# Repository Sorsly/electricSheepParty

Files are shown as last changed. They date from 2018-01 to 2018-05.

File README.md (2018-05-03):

# esp
Our senior design project, Electronic Sheep Party.
## Steps to Run
* Turn on LAN (Make sure all bots are configured to connect)
* Set up camera above the bots
* power cycle each bot and wait for the green light to turn off
* run `putilov getIP`, wait
* run `putilov run`, select y
* Launch your two seprate game front ends
* play game

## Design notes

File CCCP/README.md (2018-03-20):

Note: The Id slice in CCCP maps integers 0->numbots to camera defined ID numbers.
      The frontend only knows the bots id in the form of the index in this ids slice
      The camera only knows the distinct id it gives the blobs it sees
      The CCCPs jobs is to keep those two numbers in check, and assign the right values to the correct index

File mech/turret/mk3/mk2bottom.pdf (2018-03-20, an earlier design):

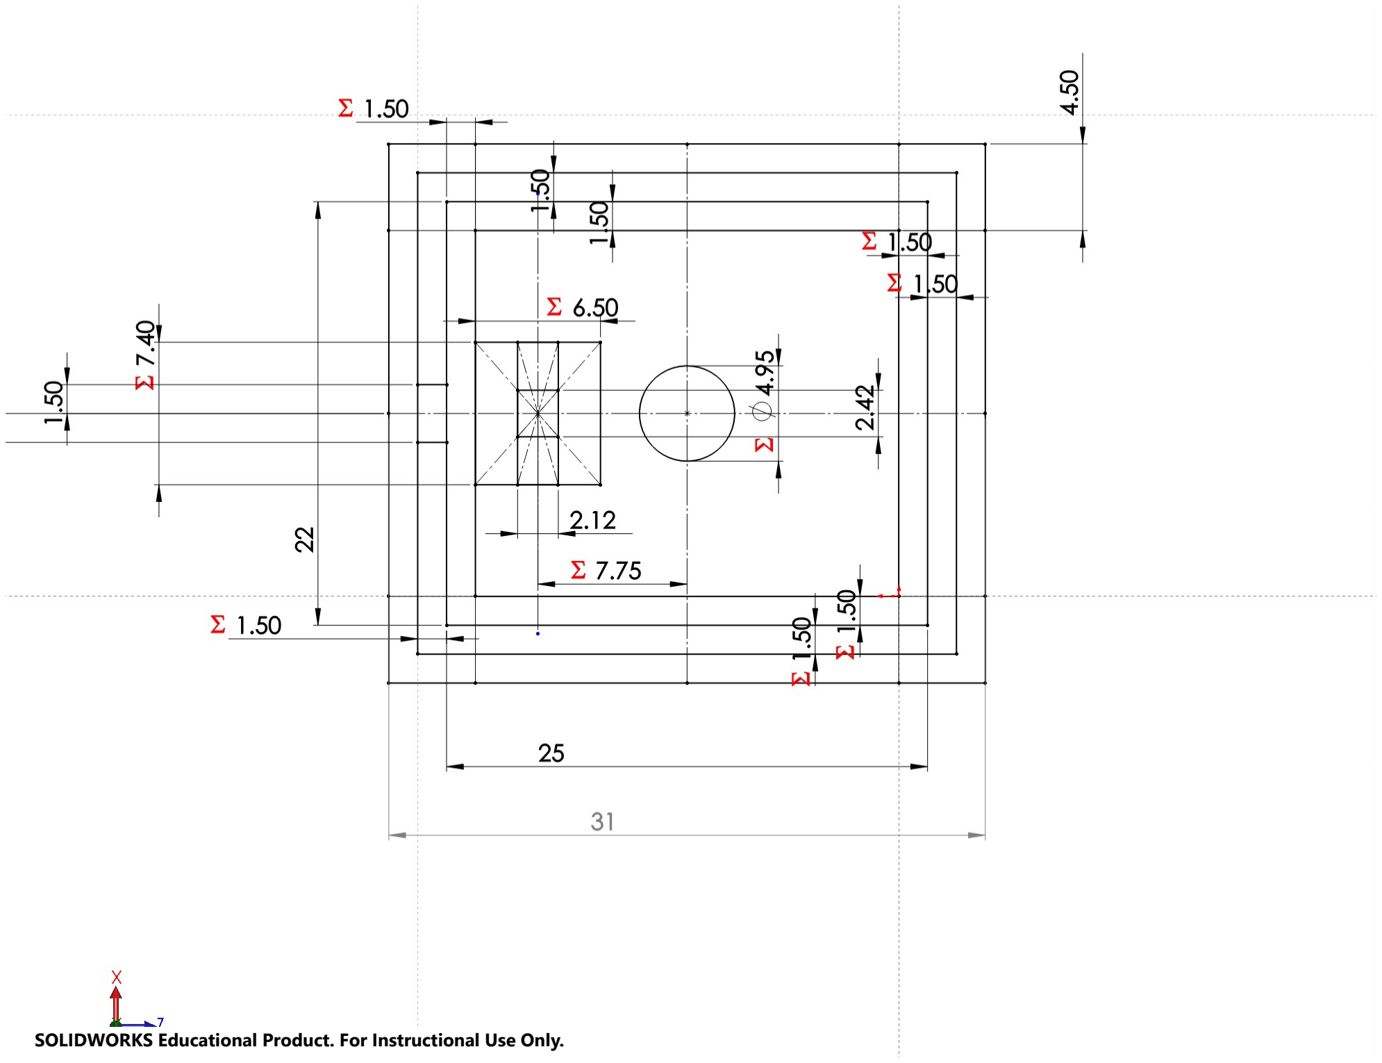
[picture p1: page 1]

SOLIDWORKS Educational Product. For Instructional Use Only.

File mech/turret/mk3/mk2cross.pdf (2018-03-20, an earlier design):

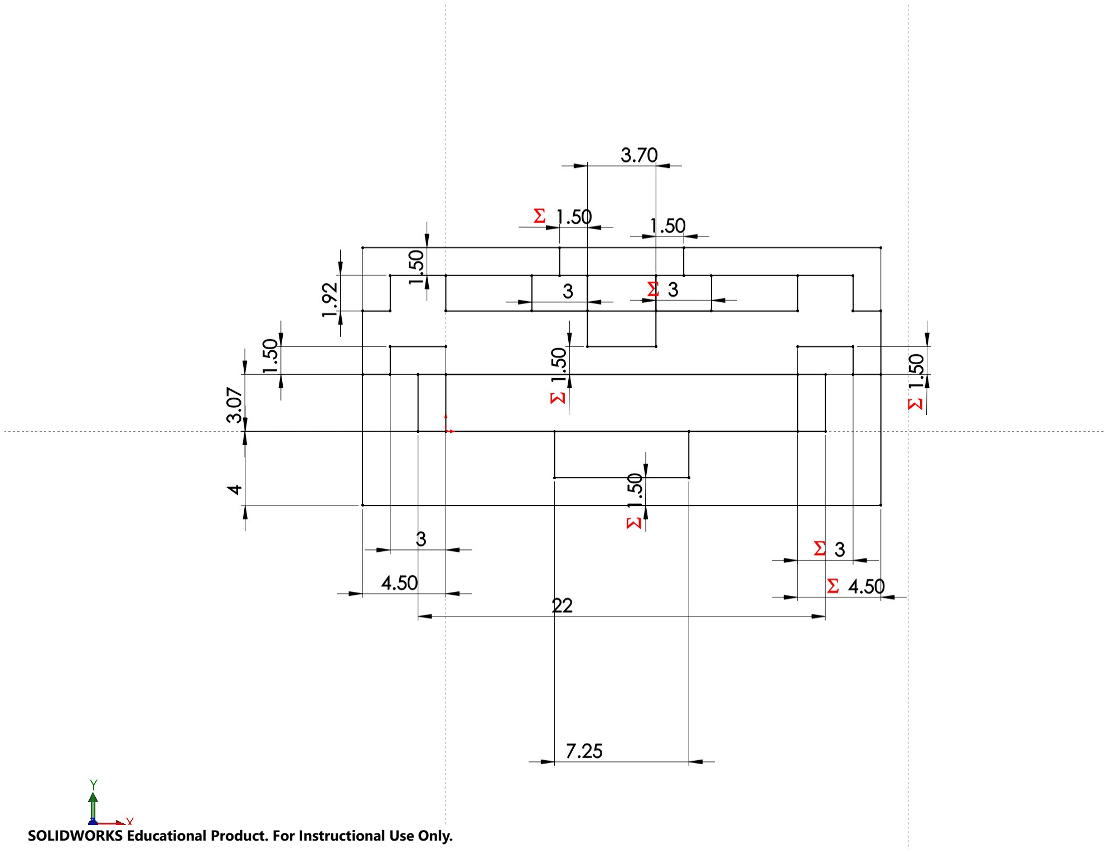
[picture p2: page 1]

SOLIDWORKS Educational Product. For Instructional Use Only.

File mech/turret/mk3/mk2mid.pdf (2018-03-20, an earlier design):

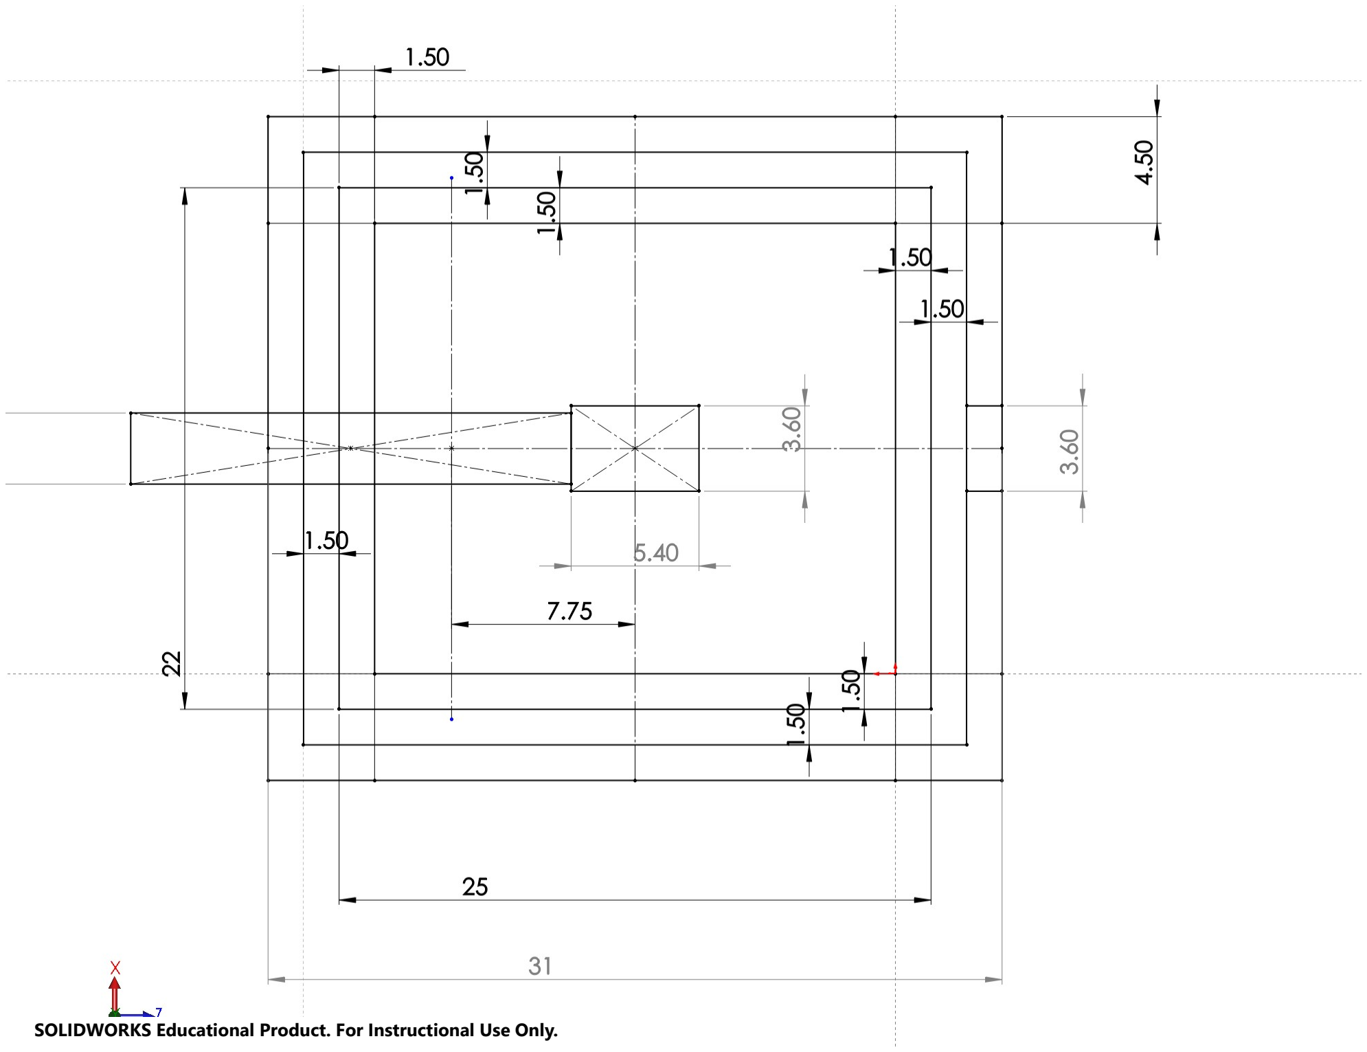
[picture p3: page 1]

SOLIDWORKS Educational Product. For Instructional Use Only.

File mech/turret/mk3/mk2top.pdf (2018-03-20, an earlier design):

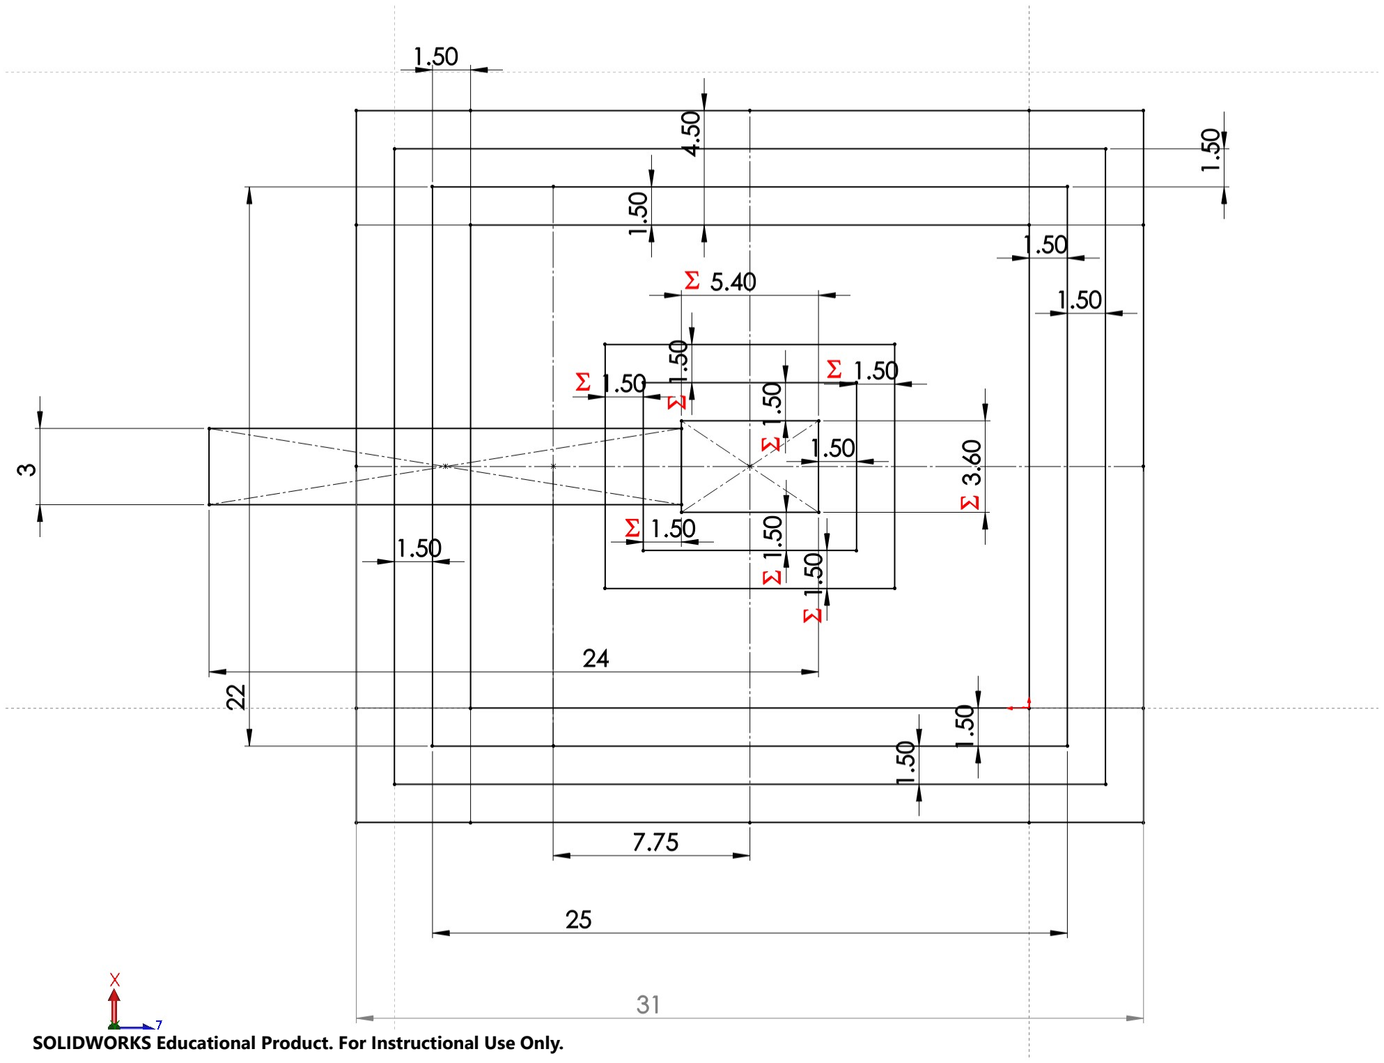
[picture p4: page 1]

SOLIDWORKS Educational Product. For Instructional Use Only.

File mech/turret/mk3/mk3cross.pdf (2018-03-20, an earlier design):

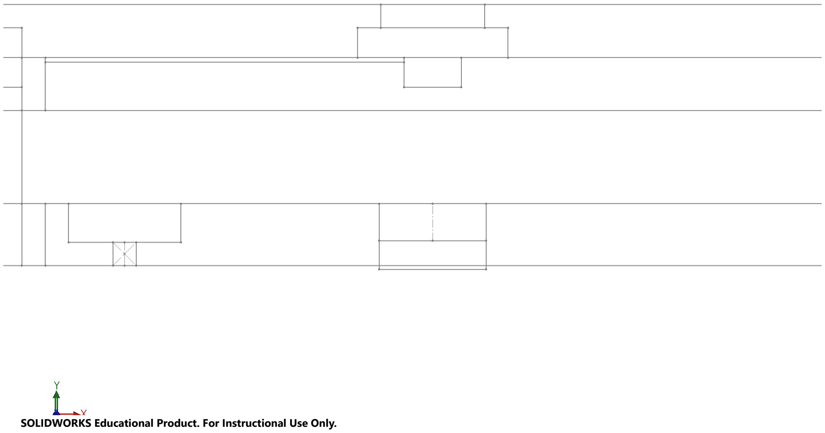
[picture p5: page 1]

SOLIDWORKS Educational Product. For Instructional Use Only.

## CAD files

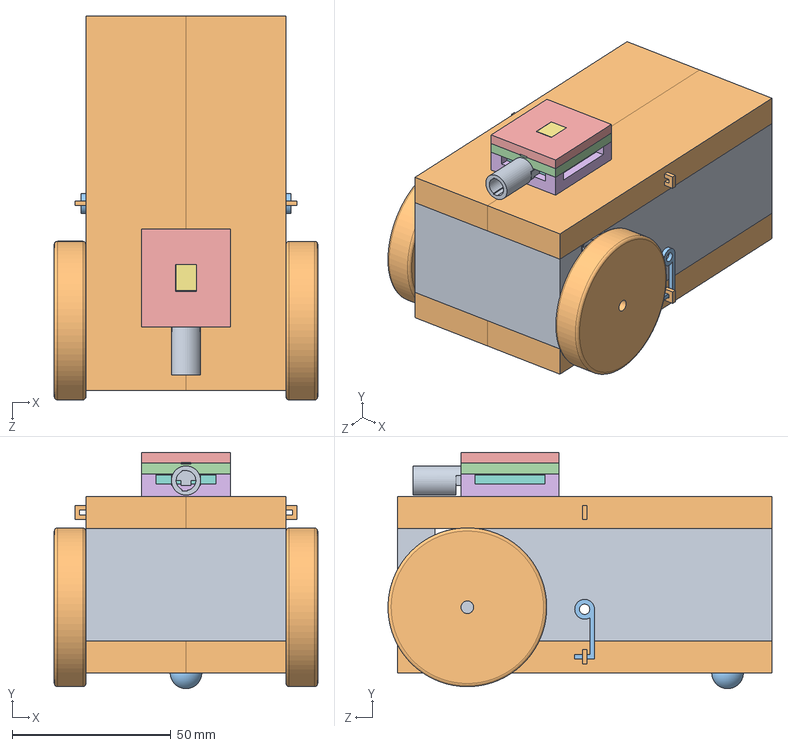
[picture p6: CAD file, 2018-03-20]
mech/asm/mechOverview.SLDASM
83.0 x 74.4 x 120.9 mm
Base 4.0 v9
pcb holder v5 x 2
J hook v2 x 2
turretBodyMiddle
turretBodyTop
turretBodyBottomSLDPRT
turretBodyTopLedCover
turretAcryllic
turretGun
drivePlaceholder x 2
thirdPlaceholder

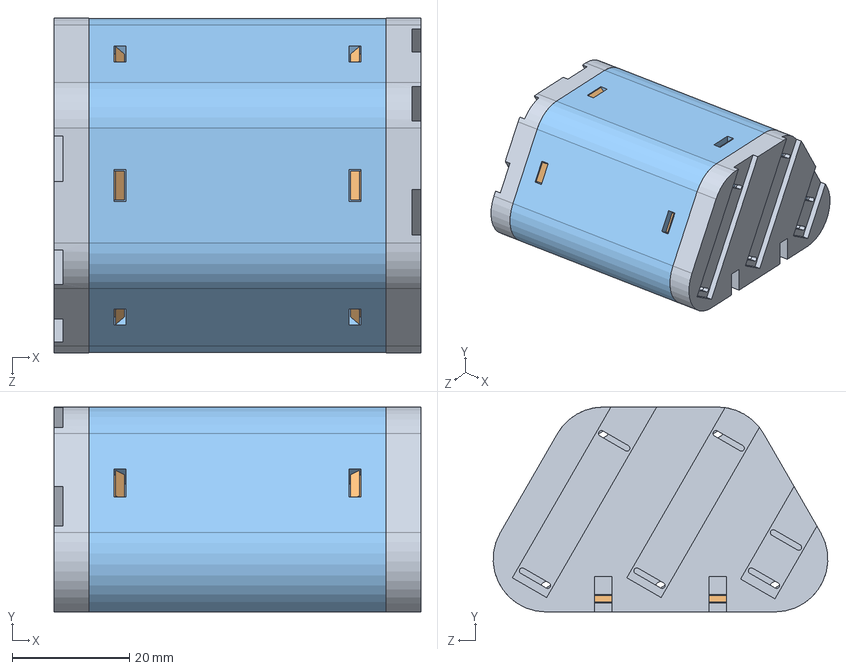
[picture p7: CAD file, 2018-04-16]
mech/body/mk3 (rev4)/batteryHousing/batteryHousingDetachable.SLDASM
62.5 x 34.9 x 57.0 mm
batteryCapDetachable x 2
batteryCant x 10
batteryShell

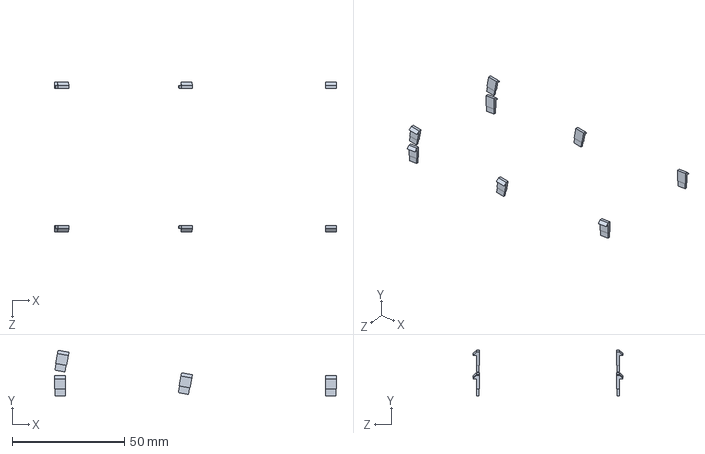
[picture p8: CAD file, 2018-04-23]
mech/body/mk3 (rev4)/bodyTop.SLDASM
125.8 x 20.3 x 67.0 mm
batteryCant x 8

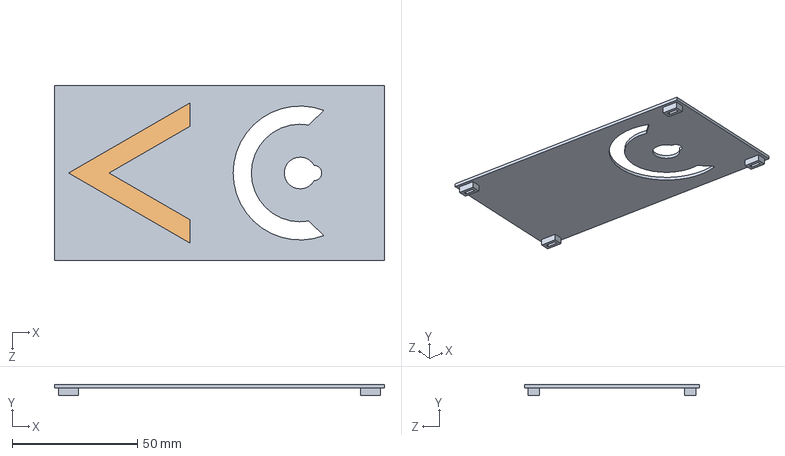
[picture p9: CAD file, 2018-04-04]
mech/body/mk3 (rev4)/bodyTopCV/bodyTopCV.SLDASM
131.9 x 4.50 x 70.0 mm
bodyTop
markCV

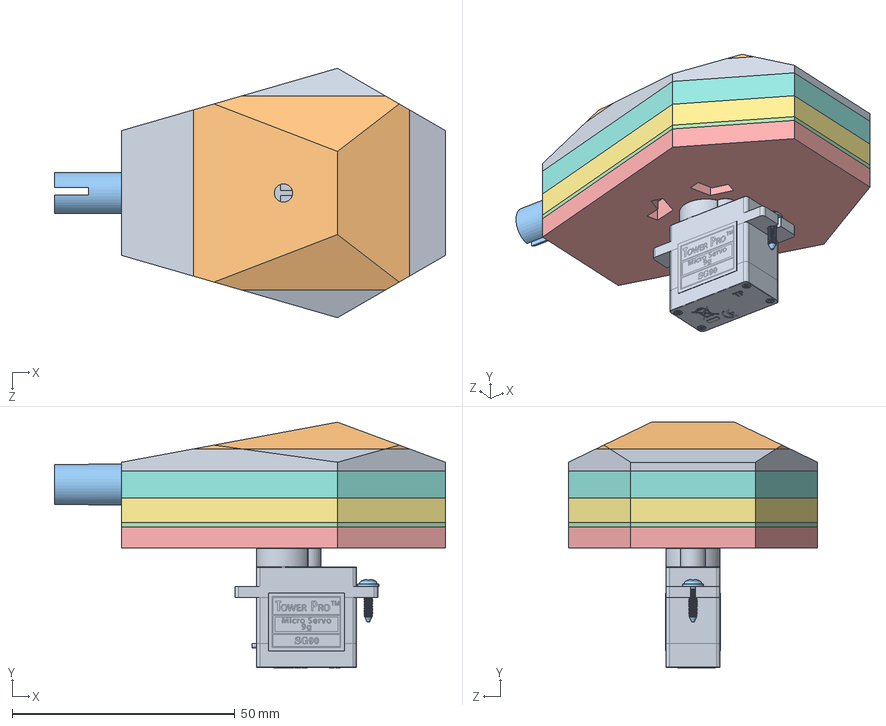
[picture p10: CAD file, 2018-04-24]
mech/turret/mk4/turret_mk4.SLDASM
87.8 x 55.2 x 56.0 mm
turretGround
quadFin
turretLevel1
turretLevel2_diffuser
turretLevel3
turretPenthouse
turretGun_fromMk3
finScrewAdjust

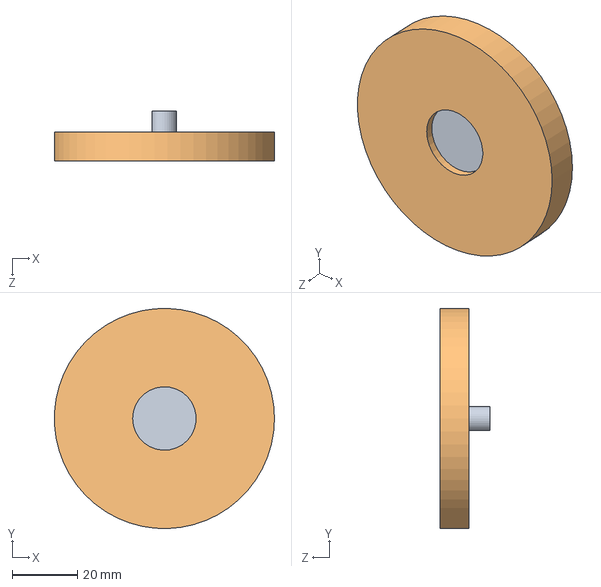
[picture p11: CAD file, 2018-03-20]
mech/wheels/mk3/wheel_mk3.SLDASM
67.4 x 67.4 x 15.4 mm
wheelCore
wheelTire

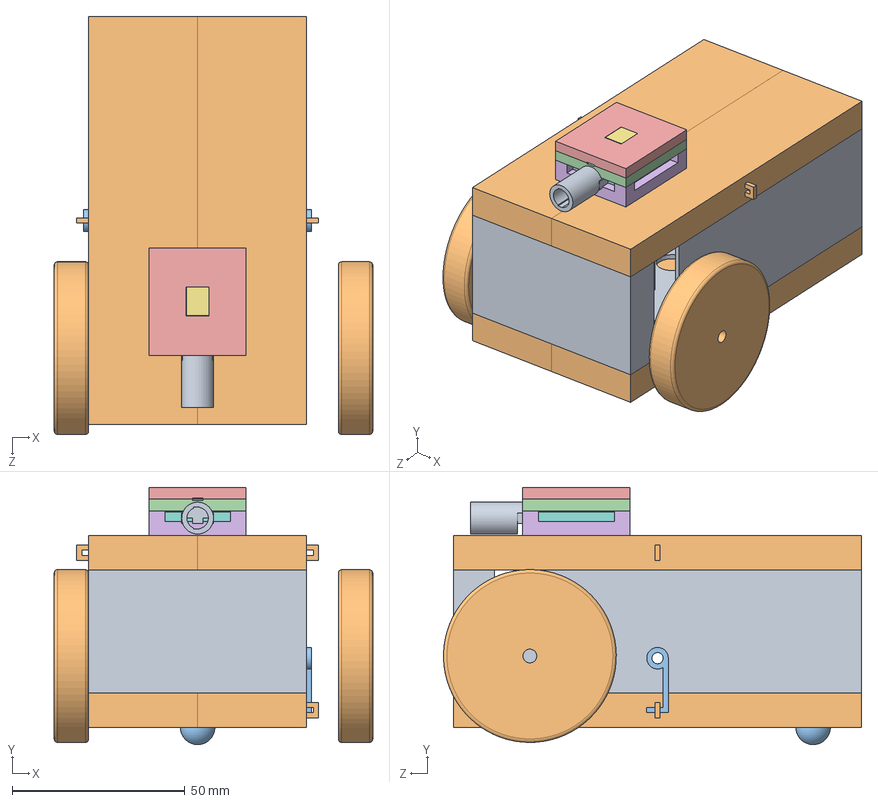
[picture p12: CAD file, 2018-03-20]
mech/asm/Backup (2) of mechOverview.SLDASM
92.2 x 74.4 x 120.9 mm
Base 4.0 v9
pcb holder v5 x 2
J hook v2 x 2
turretBodyMiddle
turretBodyTop
turretBodyBottomSLDPRT
turretBodyTopLedCover
turretAcryllic
turretGun
drivePlaceholder x 2
thirdPlaceholder

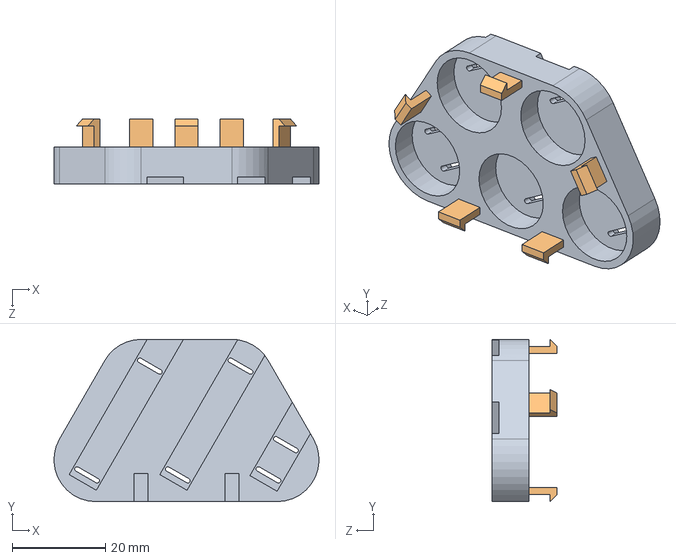
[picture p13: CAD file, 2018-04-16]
mech/body/mk3 (rev4)/batteryHousing/batteryCapDetachableInclCant.SLDASM
57.0 x 34.9 x 14.0 mm
batteryCapDetachable
batteryCant x 5

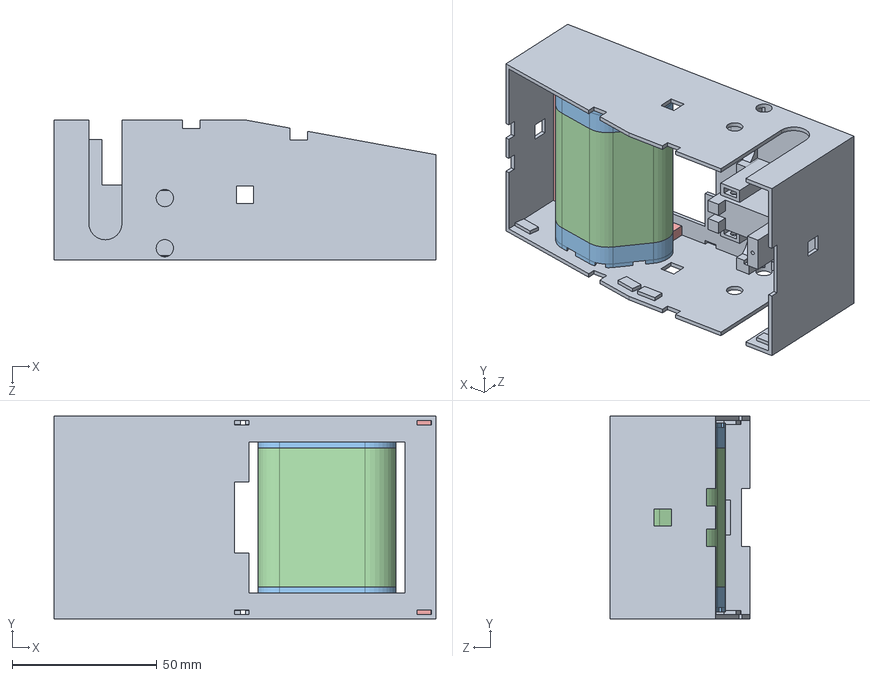
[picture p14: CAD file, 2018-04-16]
mech/body/mk3 (rev4)/fixes/cableSpacingHotFix.SLDASM
131.9 x 70.0 x 48.4 mm
batteryCap_mk3.5 x 2
batteryShell_mk3.5
slantFix

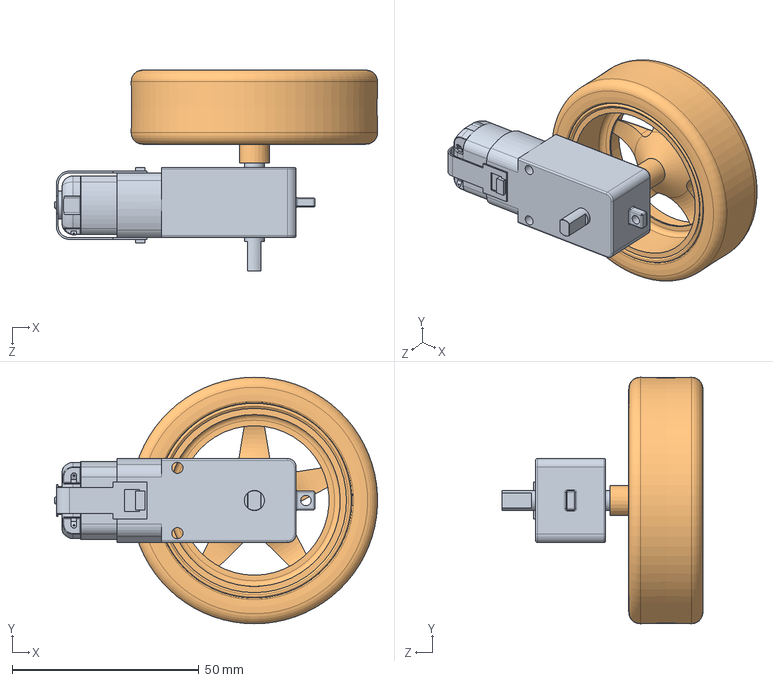
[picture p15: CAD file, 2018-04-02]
mech/misc/moto-reductor-rueda-1.snapshot.1/Moto Reductor - Rueda.SLDASM
86.5 x 66.0 x 53.9 mm
Moto Reductor 01
Rueda 01

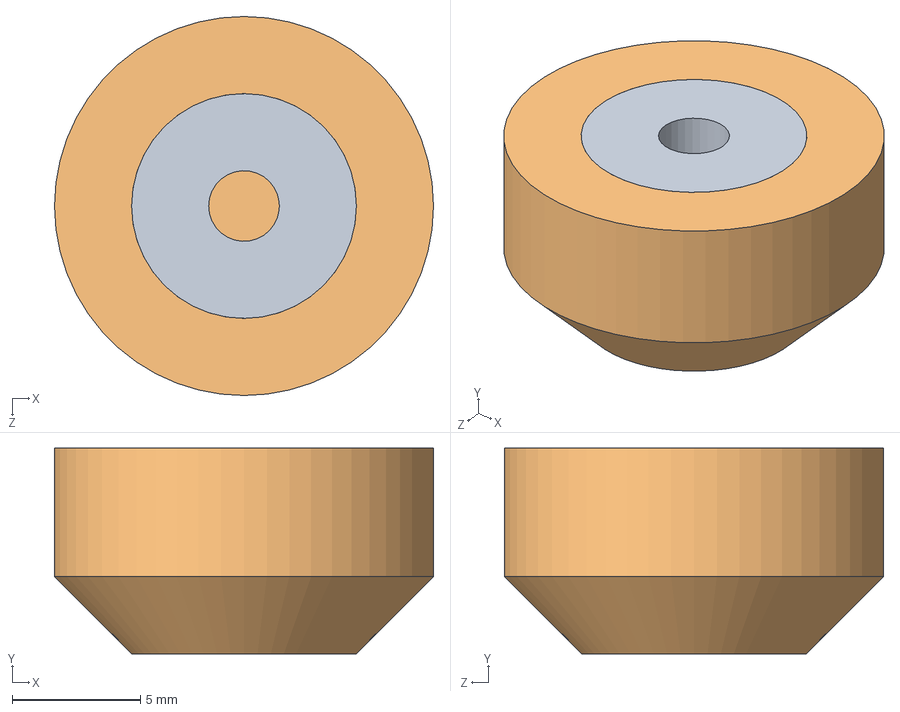
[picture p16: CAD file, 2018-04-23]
mech/wheels/mk3.5/omni/omniFoot.SLDASM
14.8 x 8.00 x 14.8 mm
maleNub
foot

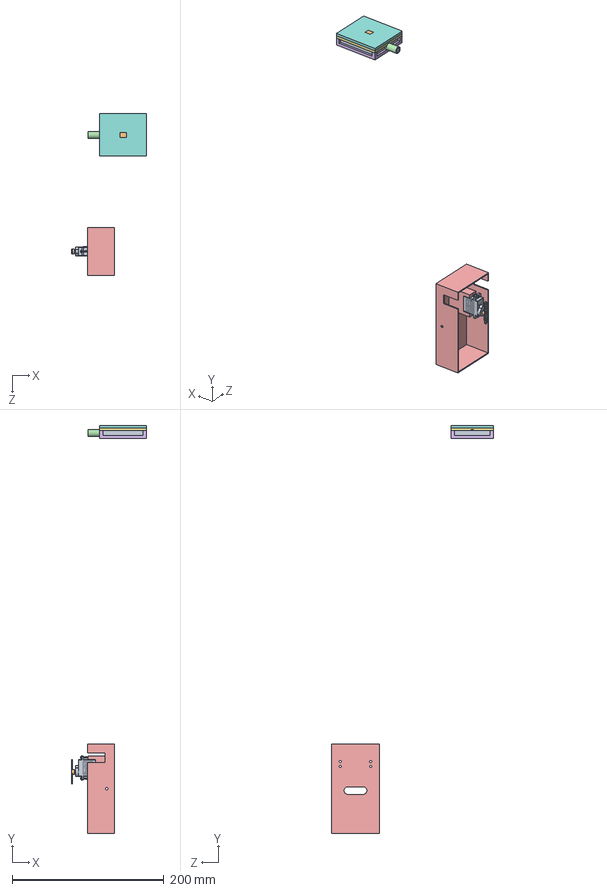
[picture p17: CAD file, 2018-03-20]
mech/asm/master.SLDASM
99.1 x 537.0 x 213.1 mm
SG90 - Micro Servo 9g - Tower Pro.1
SG90 - Micro Servo 9g - Tower Pro.3
SG90 - Micro Servo 9g - Tower Pro.5 x 2
SG90 - Micro Servo 9g - Tower Pro.6
Base 4.0 v10_mk2
turretBottom
turretMid
turretTop
turretDiffuser
turretLEDcover
Part10^turretGun

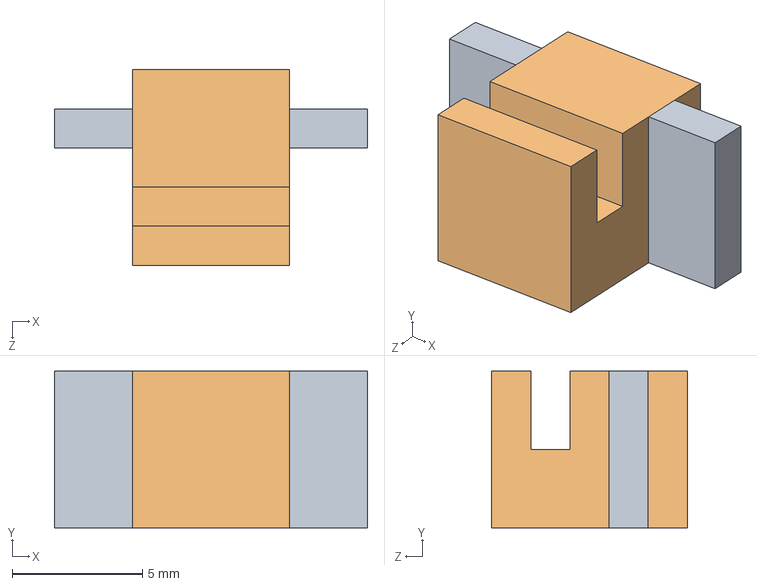
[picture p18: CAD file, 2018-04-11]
mech/body/mk3 (rev4)/attachPoint/Backup (1) of attachPointASM.SLDASM
12.0 x 6.00 x 7.50 mm
attachPoint
attachHook

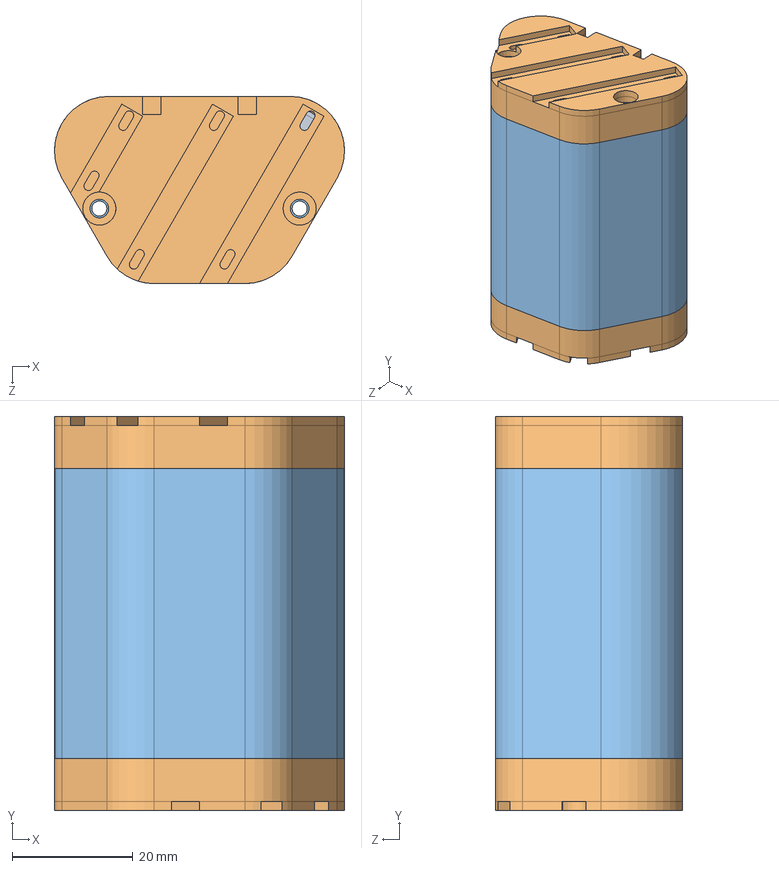
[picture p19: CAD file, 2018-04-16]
mech/body/mk3 (rev4)/batteryHousing/mk3.5/batteryHousing_mk3.5.SLDASM
48.0 x 65.2 x 31.0 mm
batteryCap_mk3.5 x 2
batteryShell_mk3.5

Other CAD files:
mech/wheels/mk3/omni/omniASM.sldasm
mech/misc/sg90-micro-servo-9g-tower-pro-1.snapshot.2/SG90 - Micro Servo 9g - Tower Pro.SLDASM
mech/misc/team/espPin.SLDASM
mech/misc/utility/aBox.SLDASM
mech/asm/Backup (1) of mechOverview.SLDASM
mech/asm/Backup (3) of mechOverview.SLDASM
mech/body/Base 2.0 v7.step
mech/body/Base 4.0 v2.step
mech/body/mk3 (rev4)/Backup (1) of bodyTop.SLDASM
mech/body/mk3 (rev4)/Backup (1) of bodyTop.sldprt
mech/body/mk3 (rev4)/Backup (1) of body_mk3.sldprt
mech/body/mk3 (rev4)/Backup (1) of frontWeightContainer.sldprt
mech/body/mk3 (rev4)/Backup (1) of omniBallCore.sldprt
mech/body/mk3 (rev4)/Backup (1) of pcbHolder_mk3.sldprt
mech/body/mk3 (rev4)/Backup (1) of protoBody.SLDASM
mech/body/mk3 (rev4)/Backup (2) of bodyTop.SLDASM
mech/body/mk3 (rev4)/Backup (2) of body_mk3.sldprt
mech/body/mk3 (rev4)/Backup (2) of frontWeightContainer.sldprt
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

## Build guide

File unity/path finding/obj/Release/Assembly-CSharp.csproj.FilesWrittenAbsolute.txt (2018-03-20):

/Users/snayha/Unity/path finding/Temp/bin/Release/Assembly-CSharp.dll.mdb
/Users/snayha/Unity/path finding/Temp/bin/Release/Assembly-CSharp.dll
/Users/snayha/Unity/path finding/obj/Release/Assembly-CSharp.dll
/Users/snayha/Unity/path finding/obj/Release/Assembly-CSharp.dll.mdb
/Users/snayha/Unity/path finding/Temp/bin/Release/UnityEngine.dll
/Users/snayha/Unity/path finding/Temp/bin/Release/UnityEditor.dll
/Users/snayha/Unity/path finding/Temp/bin/Release/UnityEngine.UIAutomation.dll
/Users/snayha/Unity/path finding/Temp/bin/Release/UnityEditor.UIAutomation.dll
/Users/snayha/Unity/path finding/Temp/bin/Release/UnityEditor.TestRunner.dll
/Users/snayha/Unity/path finding/Temp/bin/Release/UnityEngine.TestRunner.dll
/Users/snayha/Unity/path finding/Temp/bin/Release/nunit.framework.dll
/Users/snayha/Unity/path finding/Temp/bin/Release/UnityEngine.Networking.dll
/Users/snayha/Unity/path finding/Temp/bin/Release/UnityEditor.Networking.dll
/Users/snayha/Unity/path finding/Temp/bin/Release/UnityEngine.UI.dll
/Users/snayha/Unity/path finding/Temp/bin/Release/UnityEditor.UI.dll
/Users/snayha/Unity/path finding/Temp/bin/Release/UnityEngine.Timeline.dll
/Users/snayha/Unity/path finding/Temp/bin/Release/UnityEditor.Timeline.dll
/Users/snayha/Unity/path finding/Temp/bin/Release/UnityEditor.TreeEditor.dll
/Users/snayha/Unity/path finding/Temp/bin/Release/UnityEditor.GoogleAudioSpatializer.dll
/Users/snayha/Unity/path finding/Temp/bin/Release/UnityEngine.GoogleAudioSpatializer.dll
/Users/snayha/Unity/path finding/Temp/bin/Release/UnityEditor.HoloLens.dll
/Users/snayha/Unity/path finding/Temp/bin/Release/UnityEngine.HoloLens.dll
/Users/snayha/Unity/path finding/Temp/bin/Release/UnityEditor.SpatialTracking.dll
/Users/snayha/Unity/path finding/Temp/bin/Release/UnityEngine.SpatialTracking.dll
/Users/snayha/Unity/path finding/Temp/bin/Release/UnityEditor.VR.dll
/Users/snayha/Unity/path finding/Temp/bin/Release/UnityEditor.Graphs.dll
/Users/snayha/Unity/path finding/Temp/bin/Release/UnityEditor.Android.Extensions.dll
/Users/snayha/Unity/path finding/Temp/bin/Release/UnityEditor.iOS.Extensions.dll
/Users/snayha/Unity/path finding/Temp/bin/Release/UnityEditor.WebGL.Extensions.dll
/Users/snayha/Unity/path finding/Temp/bin/Release/UnityEditor.LinuxStandalone.Extensions.dll
/Users/snayha/Unity/path finding/Temp/bin/Release/UnityEditor.OSXStandalone.Extensions.dll
/Users/snayha/Unity/path finding/Temp/bin/Release/UnityEngine.Advertisements.dll
/Users/snayha/Unity/path finding/Temp/bin/Release/UnityEditor.Advertisements.dll
/Users/snayha/Unity/path finding/Temp/bin/Release/UnityEngine.Analytics.dll
/Users/snayha/Unity/path finding/Temp/bin/Release/UnityEditor.Analytics.dll
/Users/snayha/Unity/path finding/Temp/bin/Release/UnityEngine.Purchasing.dll
/Users/snayha/Unity/path finding/Temp/bin/Release/UnityEditor.Purchasing.dll
/Users/snayha/Unity/path finding/Temp/bin/Release/UnityEngine.StandardEvents.dll
/Users/snayha/Unity/path finding/Temp/bin/Release/Unity.Cecil.dll
/Users/snayha/Unity/path finding/Temp/bin/Release/Unity.SerializationLogic.dll
/Users/snayha/Unity/path finding/Temp/bin/Release/Unity.DataContract.dll
/Users/snayha/Unity/path finding/Temp/bin/Release/ExCSS.Unity.dll
/Users/snayha/Unity/path finding/Temp/bin/Release/Unity.Legacy.NRefactory.dll
/Users/snayha/Unity/path finding/Temp/bin/Release/Unity.UNetWeaver.dll
/Users/snayha/Unity/path finding/Temp/bin/Release/Unity.UNetWeaver.dll.mdb
/Users/snayha/Unity/path finding/Temp/bin/Release/Unity.CecilTools.dll
/Users/snayha/Unity/path finding/Temp/bin/Release/Unity.Cecil.Pdb.dll
/Users/snayha/Unity/path finding/Temp/bin/Release/Unity.Cecil.Mdb.dll
/Users/snayha/Unity/path finding/Temp/bin/Release/UnityEditor.iOS.Extensions.Xcode.dll
/Users/snayha/Unity/path finding/Temp/bin/Release/UnityEditor.iOS.Extensions.Xcode.xml
/Users/snayha/Unity/path finding/Temp/bin/Release/UnityEditor.iOS.Extensions.Common.dll
/Users/snayha/Unity/path finding/Temp/bin/Release/UnityEditor.iOS.Extensions.Common.dll.mdb

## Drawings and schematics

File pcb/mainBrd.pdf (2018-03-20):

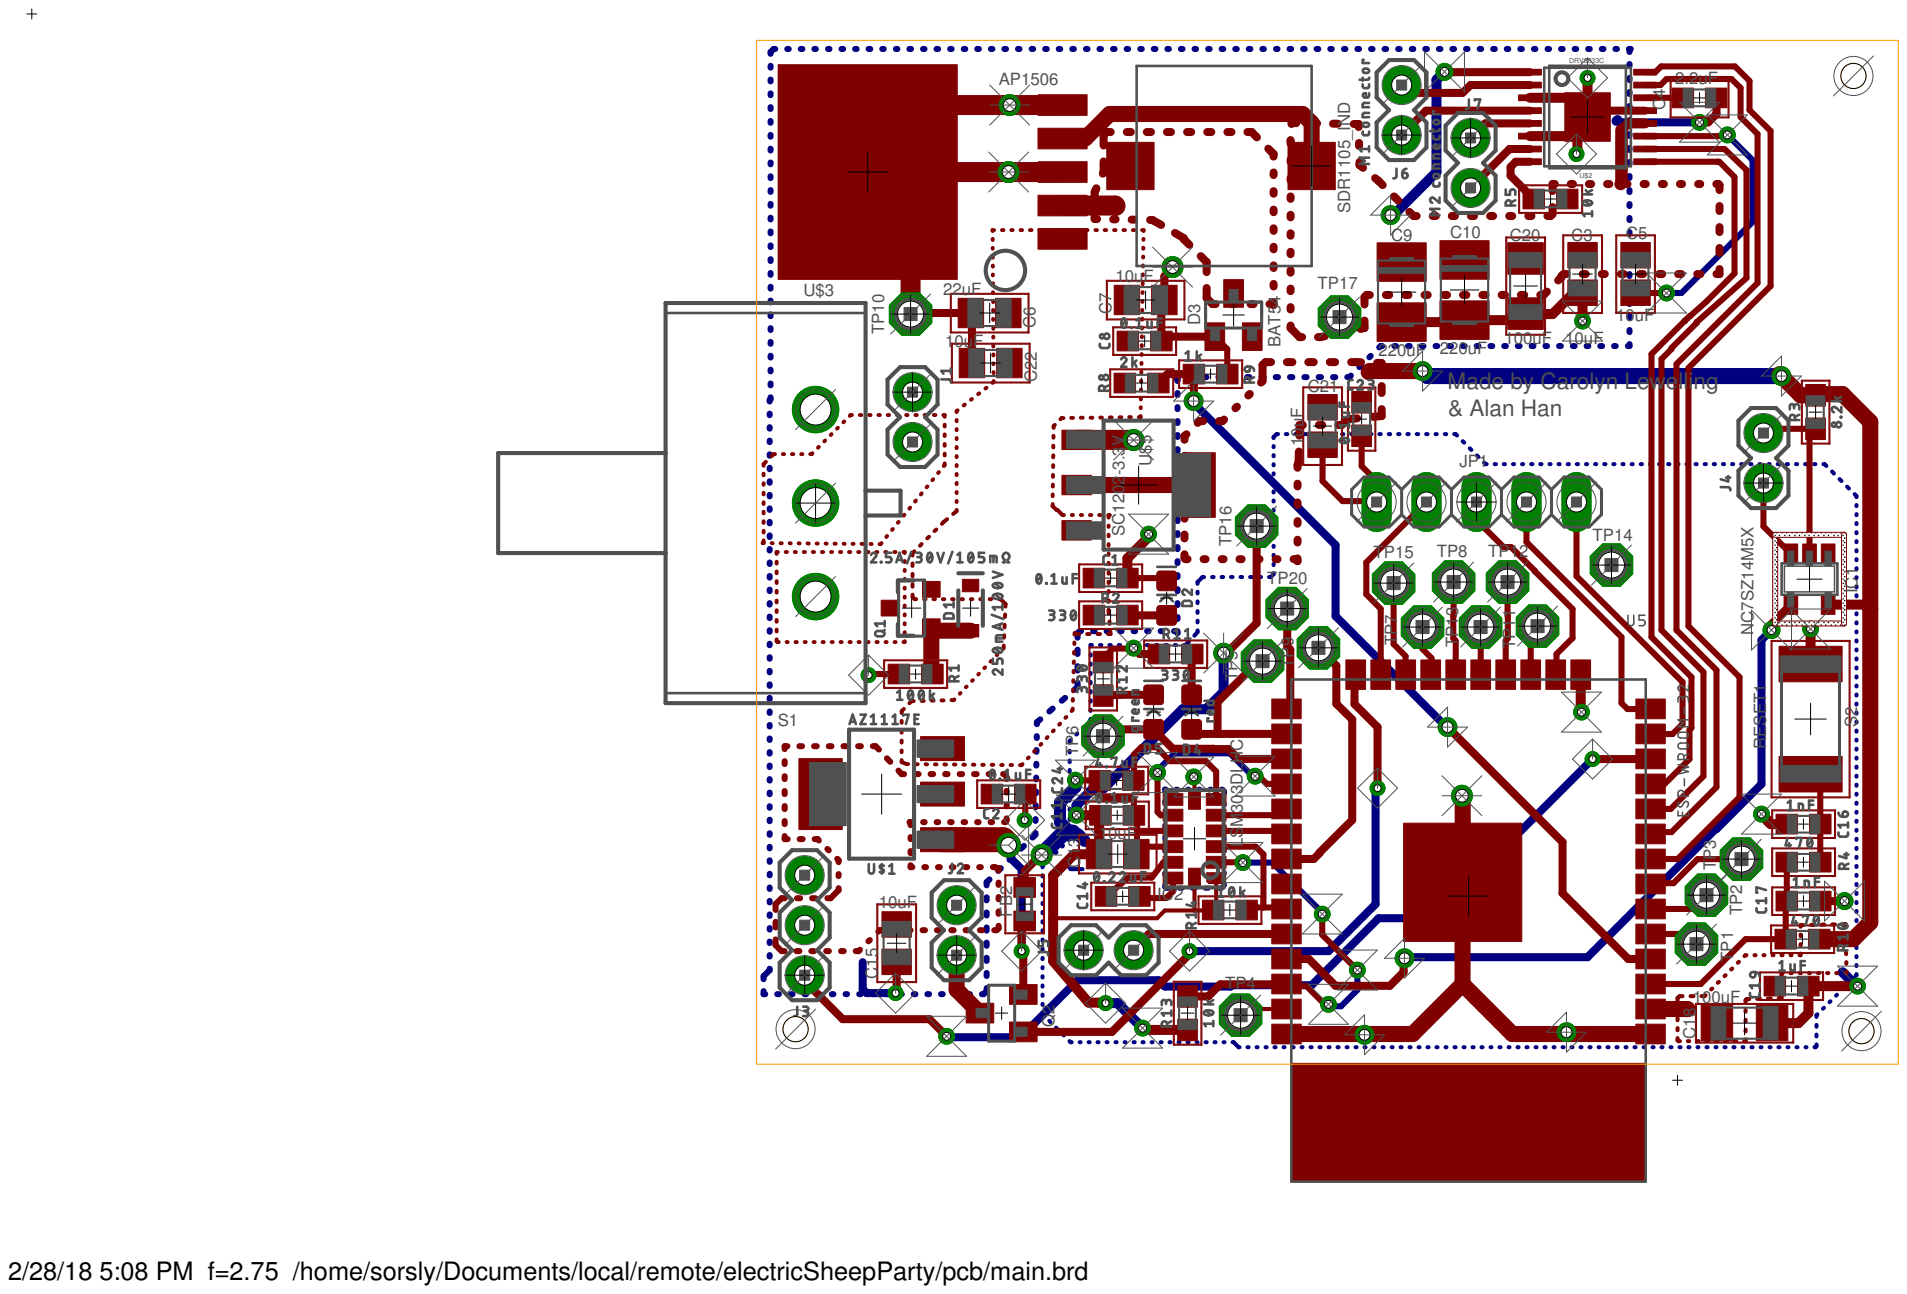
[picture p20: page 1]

SDR1105_IND Made by Carolyn Lewelling

2/28/18 5:08 PM f=2.75 /home/sorsly/Documents/local/remote/electricSheepParty/pcb/main.brd

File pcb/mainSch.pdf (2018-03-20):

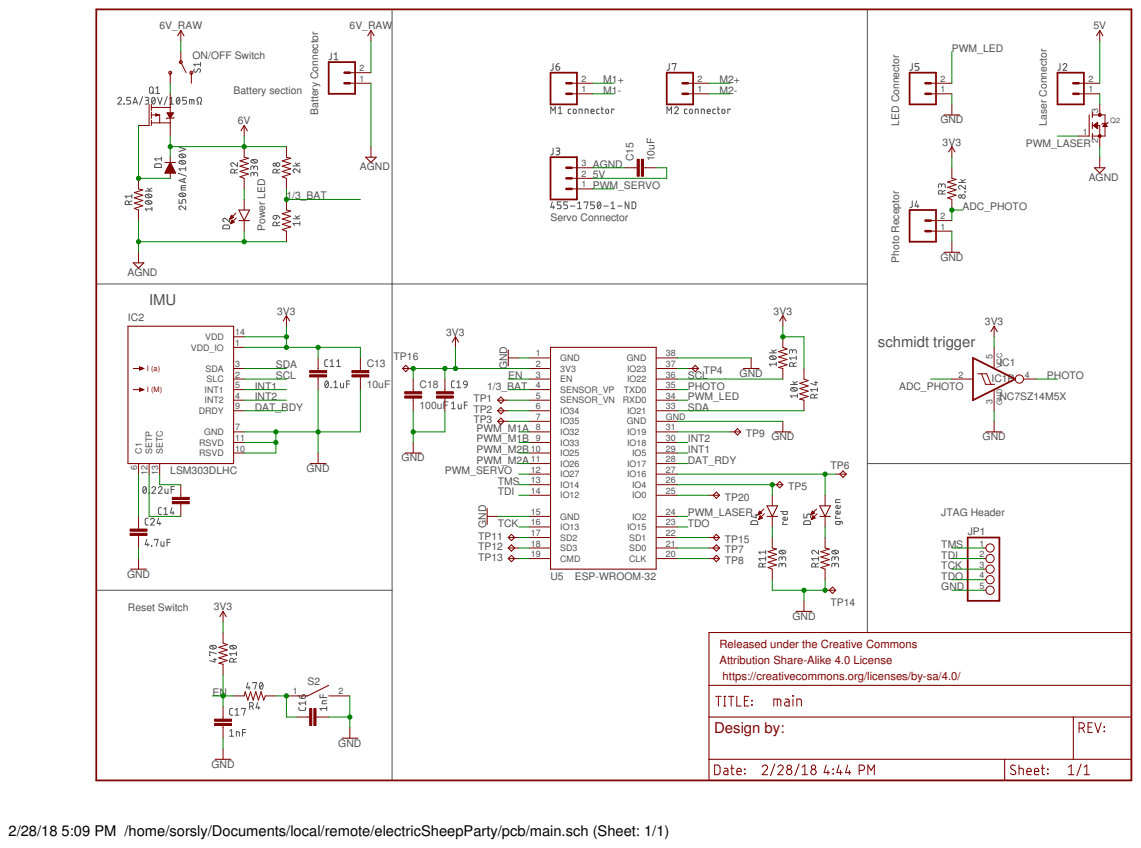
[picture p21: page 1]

Photo Receptor LED Connector 3V3

Released under the Creative Commons Attribution Share-Alike 4.0 License

https://creativecommons.org/licenses/by-sa/4.0/

2/28/18 5:09 PM /home/sorsly/Documents/local/remote/electricSheepParty/pcb/main.sch (Sheet: 1/1)

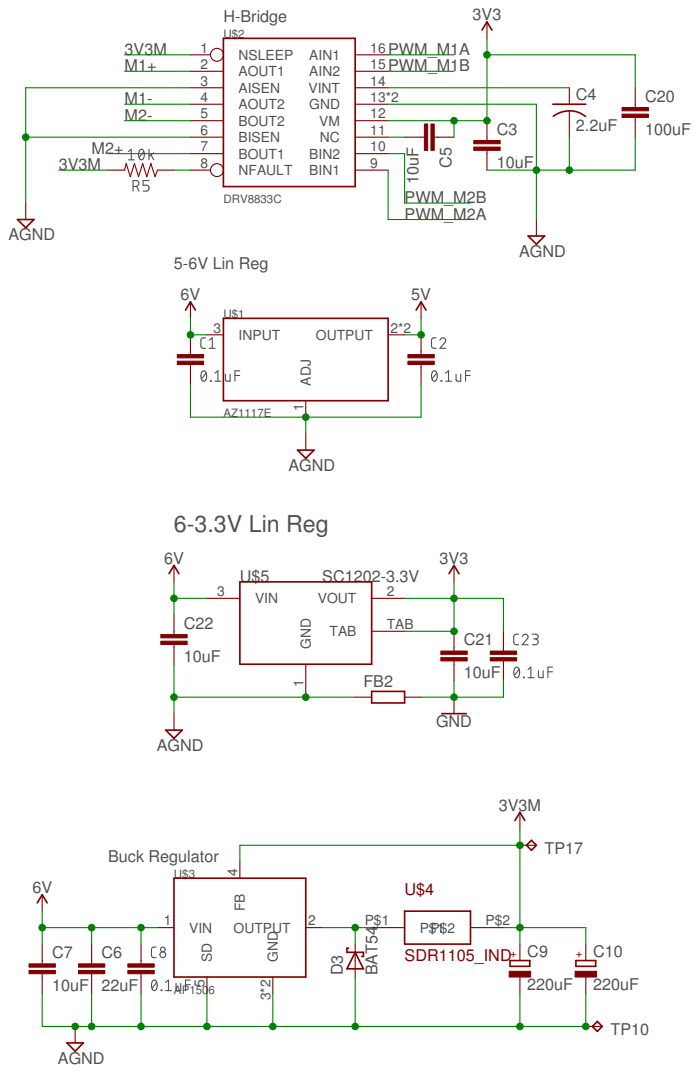
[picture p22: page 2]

Released under the Creative Commons Attribution Share-Alike 4.0 License

https://creativecommons.org/licenses/by-sa/4.0/

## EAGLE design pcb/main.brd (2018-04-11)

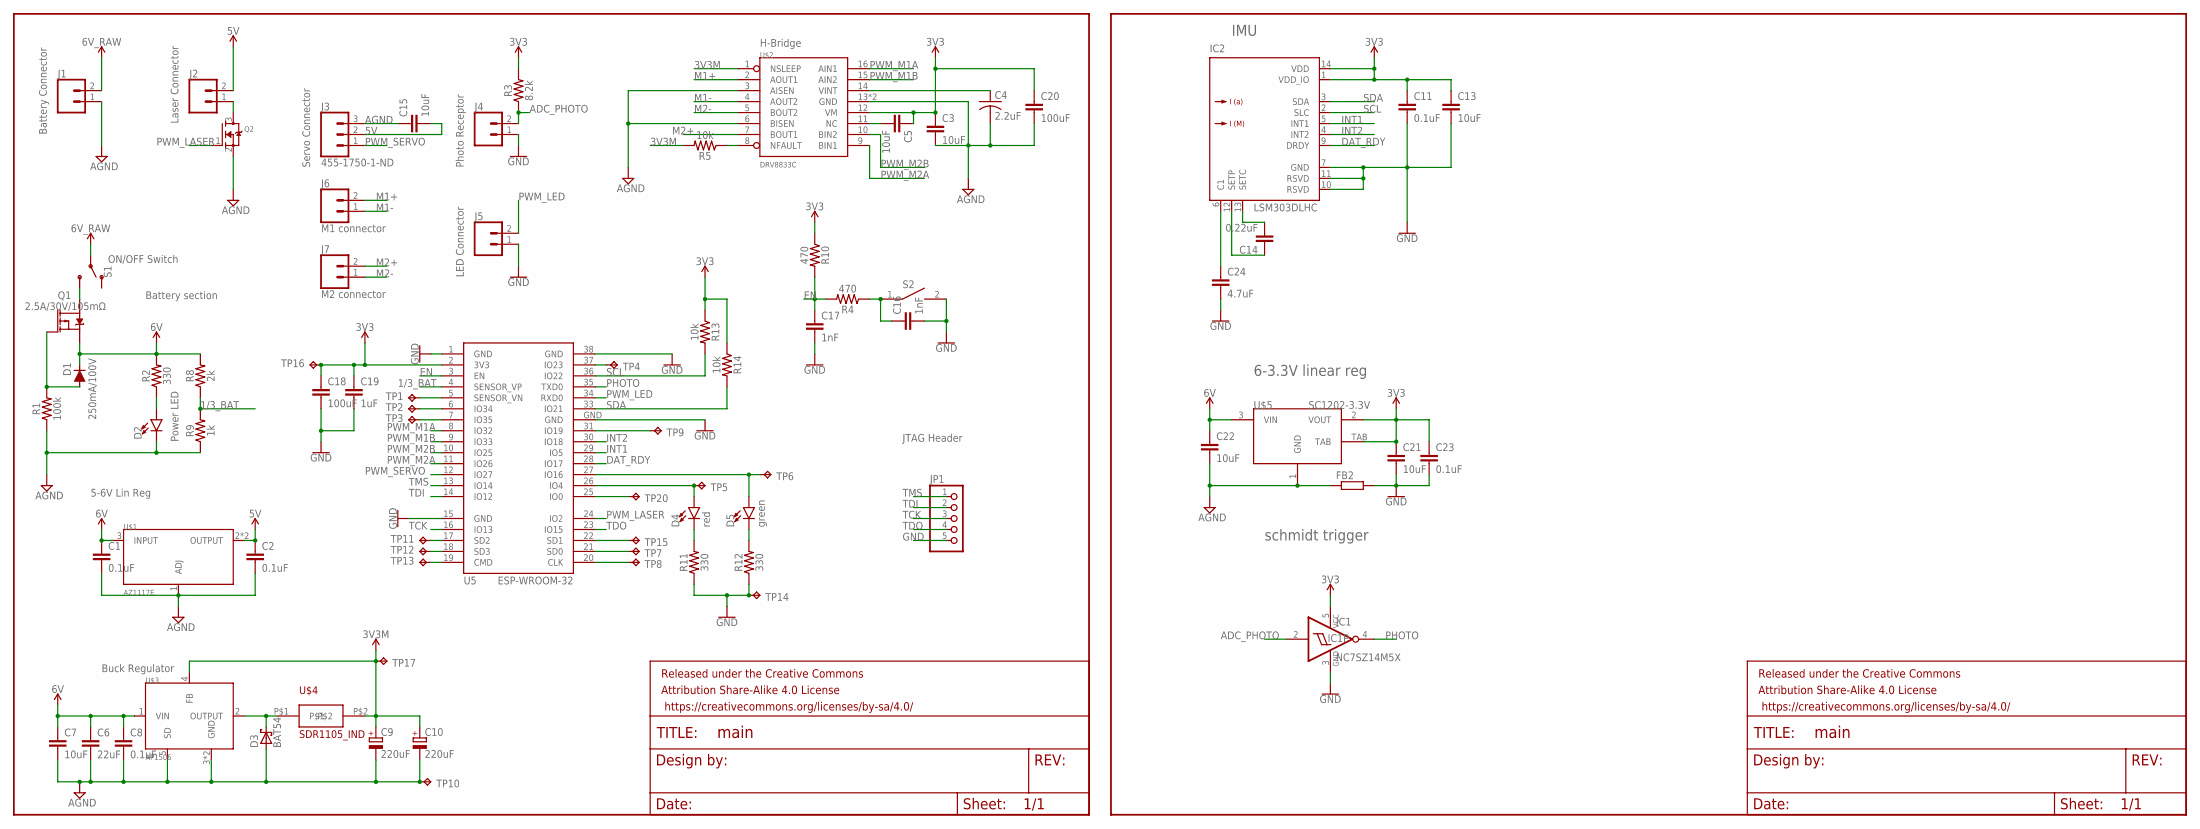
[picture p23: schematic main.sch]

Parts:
C1, C2, C8, C11, C23: 0.1uF; 0603
C3, C5, C7, C13, C15, C21, C22: 10uF; C0805
C4: 2.2uF; C0603
C6: 22uF; C0805
C9, C10: 220uF; B/3528-21R
C14: 0.22uF; 0603
C16, C17: 1nF; 0603
C18, C20: 100uF; C1206
C19: 1uF; 0603
C24: 4.7uF; 0603
D1: 250mA/100V; SOD-323
D2: LED0603; LED-0603
D3: BAT54; SOT23
D4: red; LED-0603
D5: green; LED-0603
FB2: R-EU_R0603; R0603
FRAME1, FRAME2: FRAME-LETTERNO_PACKAGE; DUMMY
IC1: NC7SZ14M5X; SOT23-5
IC2: LSM303DLHC; LGA-14
J1, J2, J4, J5: CONN_02; 1X02
J3: 455-1750-1-ND; 1X03
J6: M1 connector; 1X02
J7: M2 connector; 1X02
JP1: PINHD-1X5; 1X05
Q1: 2.5A/30V/105mΩ; SOT23-3
Q2: MOSFET-NREFLOW; SOT23
R1: 100k; 0603
R2, R11, R12: 330; 0603
R3: 8.2k; 0603
R4, R10: 470; 0603
R5, R13, R14: 10k; 0603
R8: 2k; 0603
R9: 1k; 0603
RESET1: S2; SW_2512
S1: SWITCH-SPDTRIGHTANGLESWITCH; L102021ML04Q
TP1, TP2, TP3, TP4, TP5, TP6, TP7, TP8, TP9, TP10, TP11, TP12, TP13, TP14, TP15, TP16, TP17, TP20: TPPAD1-13; P1-13
U5: ESP-WROOM-32
U$1: AZ1117E; SOT223
U$2: DRV8833C; HTSSOP-16
U$3: AP1506; TO263-5
U$4: SDR1105_IND; SDR1105
U$5: SC1202-3.3V; SOT-223

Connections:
1/3_BAT: R8.1, R9.2, U5.4 (SENSOR_VP)
3V3: C11.1, C13.1, C18.1, C19.1, C21.1, C23.1, IC1.5 (VCC), IC2.1 (VDD_IO), IC2.14 (VDD), R3.2, R10.1, R13.1, R14.1, TP16.TP, U5.2 (3V3), U$5.2 (VOUT), U$5.TAB; also elsewhere on the board
3V3M: C3.1, C5.1, C9.+, C10.+, C20.1, R5.2, TP17.TP, U$2.1 (NSLEEP), U$2.12 (VM), U$3.4 (FB), U$4.P$2
5V: C2.1, C15.2, J2.2, J3.2, U$1.2 (OUTPUT), U$1.4 (OUTPUT)
6V: C1.1, C6.1, C7.1, C8.1, C22.1, D1.C, Q1.2 (S), R2.2, R8.2, U$1.3 (INPUT), U$3.1 (VIN), U$5.3 (VIN)
6V_RAW: J1.2, S1.P$2; also elsewhere on the board
ADC_PHOTO: IC1.2 (I), J4.2, R3.1
AGND: C1.2, C2.2, C3.2, C4.2, C6.2, C7.2, C8.2, C9.-, C10.-, C15.1, C20.2, C22.2, D2.C, D3.1 (A), FB2.1, J1.1, J3.3, Q2.2 (S), R1.1, R9.1, TP10.TP, U$1.1 (ADJ), U$2.3 (AISEN), U$2.6 (BISEN), U$2.13 (GND), U$2.17 (GND), U$3.3 (GND), U$3.5 (SD), U$3.6 (GND), U$5.1 (GND); also elsewhere on the board
DAT_RDY: IC2.9 (DRDY), U5.28 (IO17)
EN: C17.1, R4.2, R10.2, U5.3 (EN)
GND: C11.2, C13.2, C16.2, C17.2, C18.2, C19.2, C21.2, C23.2, C24.2, FB2.2, IC1.3 (GND), IC2.7 (GND), IC2.10 (RSVD), IC2.11 (RSVD), J4.1, J5.1, JP1.5, R11.1, R12.1, RESET1.2, TP14.TP, U5.1 (GND), U5.15 (GND), U5.38 (GND), U5.GND; also elsewhere on the board
INT1: IC2.5 (INT1), U5.29 (IO5)
INT2: IC2.4 (INT2), U5.30 (IO18)
IO0: TP20.TP, U5.25 (IO0); also elsewhere on the board
M1+: J6.2, U$2.2 (AOUT1)
M1-: J6.1, U$2.4 (AOUT2)
M2+: J7.2, U$2.7 (BOUT1)
M2-: J7.1, U$2.5 (BOUT2)
unnamed: D1.A, Q1.1 (G), R1.2
unnamed: D2.A, R2.1
unnamed: Q1.3 (D), S1.P$3 (S)
unnamed: TP1.TP, U5.5 (SENSOR_VN)
unnamed: TP2.TP, U5.6 (IO34)
unnamed: D3.3 (C), U$3.2 (OUTPUT), U$4.P$1
unnamed: C4.1, U$2.14 (VINT)
unnamed: C5.2, U$2.11 (NC)
unnamed: J2.1, Q2.3 (D)
unnamed: C16.1, R4.1, RESET1.1
unnamed: R5.1, U$2.8 (NFAULT)
unnamed: TP3.TP, U5.7 (IO35)
unnamed: TP8.TP, U5.20 (CLK)
unnamed: D4.A, TP5.TP, U5.26 (IO4)
unnamed: TP7.TP, U5.21 (SD0)
unnamed: TP15.TP, U5.22 (SD1)
unnamed: D5.A, TP6.TP, U5.27 (IO16)
unnamed: TP11.TP, U5.17 (SD2)
unnamed: TP12.TP, U5.18 (SD3)
unnamed: TP13.TP, U5.19 (CMD)
unnamed: TP9.TP, U5.31 (IO19)
unnamed: TP4.TP, U5.37 (IO23)
unnamed: D4.C, R11.2
unnamed: D5.C, R12.2
unnamed: C14.2, IC2.13 (SETC)
unnamed: C14.1, IC2.12 (SETP)
unnamed: C24.1, IC2.6 (C1)
PHOTO: IC1.4 (O), U5.35 (TXD0)
PWM_LASER: Q2.1 (G), U5.24 (IO2)
PWM_LED: J5.2, U5.34 (RXD0)
PWM_M1A: U5.8 (IO32), U$2.16 (AIN1)
PWM_M1B: U5.9 (IO33), U$2.15 (AIN2)
PWM_M2A: U5.11 (IO26), U$2.9 (BIN1)
PWM_M2B: U5.10 (IO25), U$2.10 (BIN2)
PWM_SERVO: J3.1, U5.12 (IO27)
SCL: IC2.2 (SLC), R13.2, U5.36 (IO22)
SDA: IC2.3 (SDA), R14.2, U5.33 (IO21)
TCK: JP1.3, U5.16 (IO13); also elsewhere on the board
TDI: JP1.2, U5.14 (IO12); also elsewhere on the board
TDO: JP1.4, U5.23 (IO15); also elsewhere on the board
TMS: JP1.1, U5.13 (IO14); also elsewhere on the board

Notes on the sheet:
Battery section
JTAG Header
schmidt trigger
6-3.3V linear reg
IMU

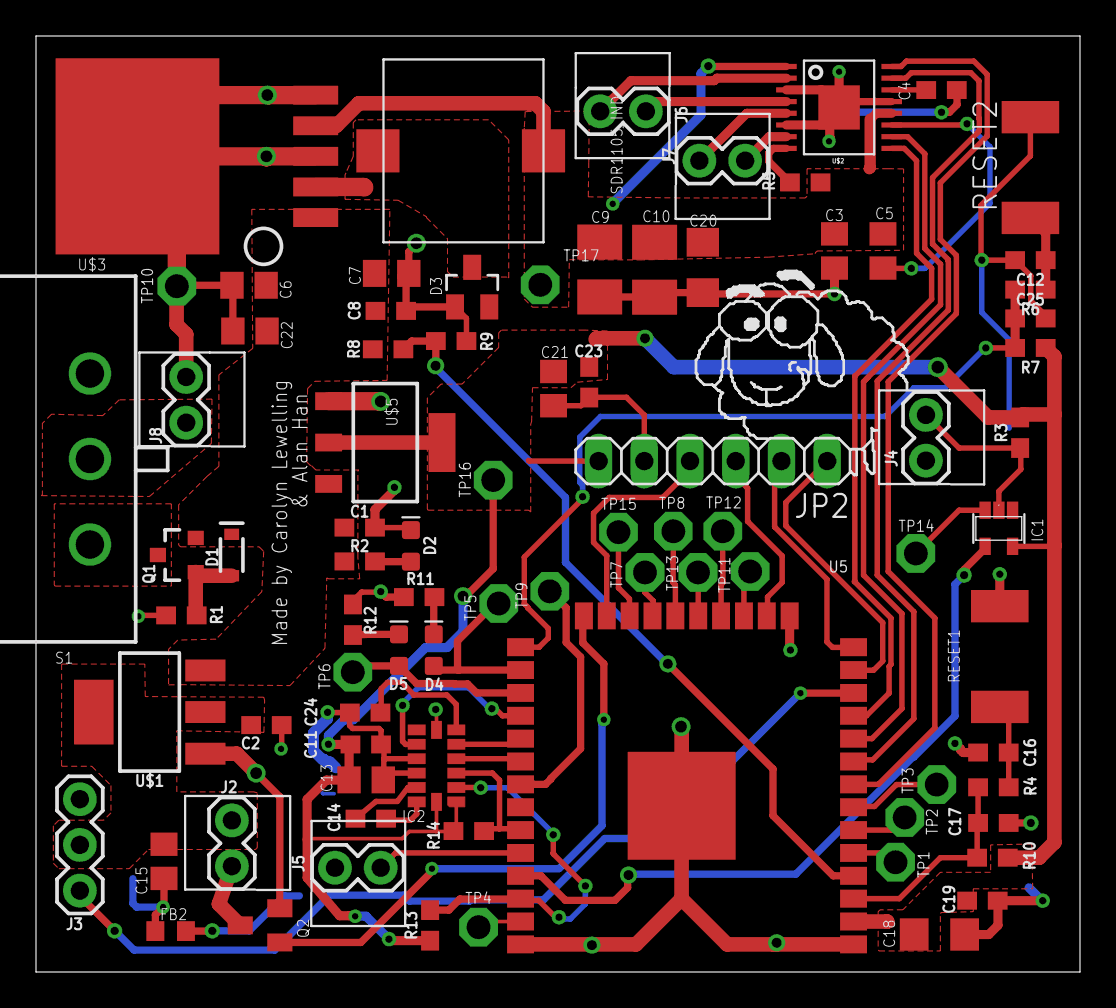
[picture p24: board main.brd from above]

Board: 2 copper layers, 58.0 x 52.0 mm, 85 parts (0 on the bottom side), 60 nets.

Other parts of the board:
C12, C25: 1nF; 0603
J8: 1X02
JP2: 1X06
R6, R7: 470; 0603
RESET2: S2; SW_2512

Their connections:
3V3: JP2.6, R7.1; also elsewhere on the board
6V_RAW: J8.1; also elsewhere on the board
AGND: J8.2; also elsewhere on the board
GND: C12.2, C25.2, JP2.5, RESET2.2; also elsewhere on the board
IO0: C25.1, R6.2, R7.2; also elsewhere on the board
unnamed: C12.1, R6.1, RESET2.1
TCK: JP2.3; also elsewhere on the board
TDI: JP2.2; also elsewhere on the board
TDO: JP2.4; also elsewhere on the board
TMS: JP2.1; also elsewhere on the board

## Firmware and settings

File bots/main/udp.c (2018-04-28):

/* Electric Sheep Party: Bot Code
 * This is the code that runs on the ESP32, that controls the bots.
 *
 * It works on a request response model. First it instantiates all of the peripherals
 * Then it connects to the wifi access point, and then enters the main loop
 * In the main loop, it constantly listens from a command from the CCCP, in the form of a udp packet
 * and then calls a move function to try and follow through with those commands. After that function
 * it then responds to the CCCP with its current state
 */
#include "udp.h"
#include "i2c.h"
#include "motor.h"
#include "ota.h"
#include <math.h>
// Tag for the main loop
static const char *TAG = "MAIN";
static const double PI = 3.141;

// These are used to connect to the wifi
static EventGroupHandle_t wifi_event_group;
ip4_addr_t ip;
char ip_str[30];
bool connected_to_ap = false;

//INPUT PINS
static const uint64_t photorec = (1 <<1);
//OUTPUT PINS
static const uint64_t topled = (1 <<3);
static const uint64_t laser = (1 <<2);
static const uint64_t debugR = (1 <<4);
static const uint64_t debugG = (1 <<16);

//The initial orientation measurment for subtracting off values
double startXorient = 0;
double startYorient = 0;

void doubleTwoBytes(double in,char * b1,char * b2){
    int16_t floored = (int16_t)in;
    *b1 = floored>>8;
    *b2 = floored & 0x00FF;

}
//Function to send the command struct to the CCCP
void send_thread(resp rsp,commands cmd) {

    //Standard C socket code
    int socket_fd;
    struct sockaddr_in sa;

    int sent_data;
    char * data_buffer = malloc(sizeof(char)*RESPSIZE);
    char bBuff1;
    char bBuff2;

    socket_fd = socket(AF_INET, SOCK_DGRAM, IPPROTO_UDP);

    if ( socket_fd < 0 ) {
        printf("socket call failed");
        exit(0);

    }

    memset(&sa, 0, sizeof(struct sockaddr_in));
    inet_pton(AF_INET, CCCPIP, &(sa.sin_addr.s_addr));
    sa.sin_family = AF_INET;
    //The port responds to the port assigned by the CCCP
    sa.sin_port = htons(cmd.portAssign);

    //Parse State
    data_buffer[0] = rsp.health;
    data_buffer[1] = rsp.accelX;
    data_buffer[2] = rsp.accelY;
    data_buffer[3] = rsp.battery;
    bBuff1 = (char)rsp.lastAngleError;
    bBuff2 = (char)(rsp.lastAngleError>>8);
    data_buffer[4] = bBuff1;
    data_buffer[5] = bBuff2;
    doubleTwoBytes(rsp.magX,&bBuff1,&bBuff2);
    data_buffer[6] = bBuff1;
    data_buffer[7] = bBuff2;
    doubleTwoBytes(rsp.magY,&bBuff1,&bBuff2);
    data_buffer[8] = bBuff1;
    data_buffer[9] = bBuff2;

    //Sending the data
    sent_data = sendto(socket_fd, data_buffer,RESPSIZE,0,(struct sockaddr*)&sa,sizeof(sa));
    if(sent_data < 0){
	    printf("send failed\n");
	    close(socket_fd);
	    exit(2);
    }

    //Closing the socket
    close(socket_fd);
}


//This function blocks, and waits for commands to come in from the designated port
void receive_thread(commands *cmd) {

    //Standard C socket code
    int socket_fd;
    struct sockaddr_in sa,ra;

    int recv_data;
    uint8_t data_buffer[15];

    socket_fd = socket(AF_INET, SOCK_DGRAM, IPPROTO_UDP);

    if ( socket_fd < 0 )
    {

        printf("socket call failed");
        exit(0);

    }

    memset(&sa, 0, sizeof(struct sockaddr_in));
    ra.sin_family = AF_INET;
    //Recieve on any adress that htis bot is assigned too
    ra.sin_addr.s_addr = htonl(INADDR_ANY);
    //All of the bots listen in at this hard coded value
    ra.sin_port = htons(RECEIVER_PORT_NUM);


    //Block until a connection
    if (bind(socket_fd, (struct sockaddr *)&ra, sizeof(struct sockaddr_in)) == -1){
    close(socket_fd);
    exit(1);
    }

    //Recieve
    recv_data = recv(socket_fd,data_buffer,sizeof(data_buffer),0);
    if(recv_data > 0)
    {
        data_buffer[recv_data] = '\0';
    }
    close(socket_fd);
    //Place the raw data into the command structure
//This is a utility function that takes the raw data and puts it into the command structure
//    void parsecommands(char * raw, commands * cmd){
    cmd->sheepf = data_buffer[0];
    cmd->relDesX = (int16_t)(data_buffer[1] | (data_buffer[2] << 8));
    cmd->relDesY = (int16_t)(data_buffer[3] | (data_buffer[4] << 8));
    cmd->servoAngle = data_buffer[5];
    cmd->portAssign= (uint16_t)(data_buffer[6] | (data_buffer[7] << 8));
    cmd->camorient = (uint16_t)(data_buffer[8] | (data_buffer[9] << 8));
    cmd->twiddleL = data_buffer[10];
    cmd->twiddleR = data_buffer[11];
    cmd->K_pt = data_buffer[11];
    cmd->K_pa = data_buffer[12];
    cmd->K_dt = data_buffer[13];
    cmd->K_da = data_buffer[14];
//   }

}


//This is a special handler function used by the esp-idf api to dictate how the not connects to the wifi.
//Full documentation on how this function needs to work can be found in the esp-idf site
static esp_err_t cust_wifi_event_handler(void *ctx, system_event_t *event)
{
    switch (event->event_id) {
        case SYSTEM_EVENT_STA_START:
            ESP_ERROR_CHECK(esp_wifi_connect());
            break;
        case SYSTEM_EVENT_STA_GOT_IP:
        	xEventGroupSetBits(wifi_event_group, CONNECTED_BIT);
            ip = event->event_info.got_ip.ip_info.ip;
            inet_ntop(AF_INET,&ip,ip_str,30);
            connected_to_ap = true;
            break;
        case SYSTEM_EVENT_STA_DISCONNECTED:
            ESP_ERROR_CHECK(esp_wifi_connect());
            xEventGroupClearBits(wifi_event_group, CONNECTED_BIT);
            break;
        default:
            break;
    }
    return ESP_OK;
}


//Initializes the wifi
void init_wifi(void)
{
    tcpip_adapter_init();
    wifi_event_group = xEventGroupCreate();
    ESP_ERROR_CHECK( esp_event_loop_init(cust_wifi_event_handler, NULL) );

    wifi_init_config_t cfg = WIFI_INIT_CONFIG_DEFAULT();
    ESP_ERROR_CHECK( esp_wifi_init(&cfg) );
    ESP_ERROR_CHECK( esp_wifi_set_storage(WIFI_STORAGE_RAM) );
    wifi_config_t wifi_config = {
        .sta = {
            .ssid = "Sliva",
            .password = "plumsaretasty",
            .scan_method = WIFI_FAST_SCAN,
            .sort_method = WIFI_CONNECT_AP_BY_SIGNAL,
            .threshold.rssi = CONFIG_FAST_SCAN_MINIMUM_SIGNAL,
            .threshold.authmode = WIFI_AUTH_WPA2_PSK,
        },
    };
    ESP_ERROR_CHECK( esp_wifi_set_mode(WIFI_MODE_STA) );
    ESP_ERROR_CHECK( esp_wifi_set_config(ESP_IF_WIFI_STA, &wifi_config) );
    ESP_ERROR_CHECK( esp_wifi_start() );

}

double angleBetween(double X,double Y, double hyp, double theta){
    double dot = X*cos(theta) + Y*sin(theta);
    double retTheta = acos(dot/hyp);
    if(X*sin(theta) - Y*cos(theta) > 0){
        retTheta = - retTheta;
    }
    return retTheta;
}

//This is the function that does all the lifting of taking the command, doingin things with it,
// And loading the state with the proper values
void move(commands * cmd, resp *state,botmemory * mem){
    //Set Sheeps Peripherals
    fire_laser(cmd->sheepf & 0x08);
    set_angle((uint32_t)cmd->servoAngle);
    top_on(cmd->sheepf & 0x10);
    canhit(&(state->health));
    //Not move command
    if(cmd->relDesX == 0 && cmd->relDesY == 0){
        left_ctl(true,0);
        right_ctl(true,0);
        return;
    }
    //Calculate Desired Angle
    double des_angle=atan2(-cmd->relDesY,cmd->relDesX);
    if (des_angle<0){
        des_angle+=2*PI;
    }
    //PD values
    double curr_angle=cmd->camorient*PI/180;//adjust for camera's angle
    double x2=pow(cmd->relDesX,2);
    double y2=pow(cmd->relDesY,2);
    double transErr = sqrt(x2+y2);
    double angleErr = angleBetween(cmd->relDesX,-cmd->relDesY,transErr,curr_angle);
    double vTrans = transErr - mem->lastTransError;
    double vAngle = angleErr - mem->lastAngleError;
    double K_pt = -(100.0/cmd->K_pt)*100.0/800;
    double K_pa = -(100.0/cmd->K_pa)*100.0/PI;
    double K_dt = -(100.0/cmd->K_dt)*100.0/800;
    double K_da = -(100.0/cmd->K_da)*100.0/PI;
    double U_t = 0;
    double U_a = 0;
    double motorL = 0;
    double motorR = 0;

    // Control Block
    if (abs(angleErr)>5 || transErr>25){
        U_t = K_pt*transErr + K_dt*vTrans;
        U_a = K_pa*angleErr + K_da*vAngle;
        motorL = U_t + U_a;
        motorR = U_t - U_a;
        if(abs(motorR + cmd->twiddleR )> 100){
            motorR = 100 - cmd->twiddleR;
        }
        if(abs(motorL + cmd->twiddleL)> 100){
            motorL = 100 - cmd->twiddleL;
        }
        if(motorR > 0){
            right_ctl(true,cmd->twiddleR + motorR);
        }else{
            right_ctl(false,cmd->twiddleR - motorR);
        }
        if(motorL > 0){
            left_ctl(true,cmd->twiddleL + motorL);
        }else{
            left_ctl(false,cmd->twiddleL - motorL);
        }


    }else{
        left_ctl(true,0);
        right_ctl(true,0);
    }
    state->lastAngleError = (uint16_t)(abs(angleErr*180/PI));
    printf("%f,%f,%f,%f,%f,%f,%f",motorR,motorL,U_a,U_t,vAngle,transErr,vTrans);
    mem->lastAngleError = angleErr;
    mem->lastTransError = transErr;
    //turn right
    //left_ctl(false,100);
    //right_ctl(true,cmd->twiddleL);

    //turn left
    //left_ctl(true, 100);
    //right_ctl(false, cmd->twiddleR);

    //forward
    //left_ctl(true,cmd->twiddleL);
    //right_ctl(true,cmd->twiddleR);
}

//Initializes the proper pins as inputs and outputs
void init_gpio(){
    gpio_config_t io_conf;
    io_conf.intr_type = GPIO_PIN_INTR_DISABLE;
    io_conf.mode = GPIO_MODE_OUTPUT;
    io_conf.pin_bit_mask = (topled|laser|debugG|debugR);
    io_conf.pull_down_en = 0;
    io_conf.pull_up_en = 0;
    gpio_config(&io_conf);

    io_conf.intr_type = GPIO_PIN_INTR_POSEDGE;
    io_conf.pin_bit_mask = photorec;
    io_conf.mode = GPIO_MODE_INPUT;
    io_conf.pull_up_en = 1;
    gpio_config(&io_conf);

}

//the main. Is called on bot startup
void app_main() {


    //The commands of the bot and the state of the bot. Dictate the bots movements
    commands * nextCommands = malloc(sizeof(commands));
    resp * state = malloc(sizeof(resp));
    botmemory * mem = malloc(sizeof(botmemory));


    state->health = 10;
    //init nvs_flash. NVS flash is used by the wifi to save configurations, making it faster to connect
    esp_err_t nvsret = nvs_flash_init();

    if (nvsret == ESP_ERR_NVS_NO_FREE_PAGES) {
        ESP_ERROR_CHECK(nvs_flash_erase());
        nvsret = nvs_flash_init();
    }

    //Initializing things
    init_wifi();
    // Wait for when the bot has connected to the AP
    while(!connected_to_ap){}
 //   init_i2c();
    init_turret(&(state->health));
    init_motors();
    init_gpio();

    //Main control loop which blocks for commands, and then responds with state
    while(true) {
        receive_thread(nextCommands);
        if (nextCommands->sheepf & 0x01) {
            top_on(nextCommands->sheepf & 0x10);
            mem->lastTransError = sqrt(pow(nextCommands->relDesX, 2) + pow(nextCommands->relDesY, 2));
            mem->lastAngleError = angleBetween(nextCommands->relDesX,
                                               nextCommands->relDesY,
                                               mem->lastTransError,
                                               nextCommands->camorient);
        }else if (nextCommands->sheepf & 0x40){
            top_on(false);
            ota_example_task(wifi_event_group);
        }else {
            move(nextCommands, state, mem);
        }
        send_thread(*state,*nextCommands);
        if(nextCommands->sheepf &  0x20){
            break;
        }
        if(state->health < 1){
            break;
        }
    }
    top_on(false);
    left_ctl(true,0);
    right_ctl(true,0);

}

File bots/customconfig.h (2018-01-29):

#define PIN_SDA 21
#define PIN_SCL 22
#define PIN_SERVO 20
#define V_REF 1100
#define PIN1_MOTOR_1 15
#define PIN2_MOTOR_1 16
#define PIN1_MOTOR_2 17
#define PIN2_MOTOR_2 18
#define PIN_RECEP ADC_CHANNEL_6 //GPIO 34

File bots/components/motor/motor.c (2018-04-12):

/* functions for controlling the motors
 *
 *
 */

#include "motor.h"

static const char *TAG = "MOTOR";
#define PIN1_MOTOR_1 32
#define PIN2_MOTOR_1 33
#define PIN1_MOTOR_2 26
#define PIN2_MOTOR_2 25


//Initialize the motos
void init_motors(){
	ESP_ERROR_CHECK(mcpwm_gpio_init(MCPWM_UNIT_0, MCPWM0A, PIN1_MOTOR_1));
	ESP_ERROR_CHECK(mcpwm_gpio_init(MCPWM_UNIT_0, MCPWM0B, PIN2_MOTOR_1));
	
	ESP_ERROR_CHECK(mcpwm_gpio_init(MCPWM_UNIT_0, MCPWM1A, PIN1_MOTOR_2));
	ESP_ERROR_CHECK(mcpwm_gpio_init(MCPWM_UNIT_0, MCPWM1B, PIN2_MOTOR_2));

	mcpwm_config_t conf0;
	conf0.frequency = 100;
	conf0.cmpr_a = 0;
	conf0.cmpr_b = 0;
	conf0.duty_mode = MCPWM_DUTY_MODE_0;
	conf0.counter_mode = MCPWM_UP_COUNTER;
	mcpwm_init(MCPWM_UNIT_0, MCPWM_TIMER_0, &conf0);

	mcpwm_config_t conf1;
	conf1.frequency = 100;
	conf1.cmpr_a = 0;
	conf1.cmpr_b = 0;
	conf1.duty_mode = MCPWM_DUTY_MODE_0;
	conf1.counter_mode = MCPWM_UP_COUNTER;
	mcpwm_init(MCPWM_UNIT_0, MCPWM_TIMER_1, &conf1);

}

//Helper functions for moving right and left
void right_ctl(bool forward,uint8_t dutycycle){
    if(forward) {
        mcpwm_set_duty(MCPWM_UNIT_0, MCPWM_TIMER_0, MCPWM_OPR_A, dutycycle);
        mcpwm_set_duty(MCPWM_UNIT_0, MCPWM_TIMER_0, MCPWM_OPR_B, 0);
	}else{
        mcpwm_set_duty(MCPWM_UNIT_0, MCPWM_TIMER_0, MCPWM_OPR_A, 0);
        mcpwm_set_duty(MCPWM_UNIT_0, MCPWM_TIMER_0, MCPWM_OPR_B, dutycycle);
	}

}

void left_ctl(bool forward,uint8_t dutycycle){
	if(forward) {
        mcpwm_set_duty(MCPWM_UNIT_0, MCPWM_TIMER_1, MCPWM_OPR_A, 0);
        mcpwm_set_duty(MCPWM_UNIT_0, MCPWM_TIMER_1, MCPWM_OPR_B, dutycycle);
	}else{
        mcpwm_set_duty(MCPWM_UNIT_0, MCPWM_TIMER_1, MCPWM_OPR_A, dutycycle);
        mcpwm_set_duty(MCPWM_UNIT_0, MCPWM_TIMER_1, MCPWM_OPR_B, 0);
	}

}

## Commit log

2018-01-21 added eagle files (sch and lbr)
    [main.sch]
2018-01-23 added H-bridge
    [main.sch]
2018-01-23 added more parts, found some parts, updated BOM with more info, reorganized schematic
    [main.sch]
2018-01-24 finished hbridge and buck converter
    created part for inductor, figured out values for buck converter caps,
    and wired hbridge
    [main.brd, main.sch]
2018-01-24 updated hbridge
    [main.sch]
2018-01-24 added IMU
    [main.brd, main.sch]
2018-01-26 changed gnd symbol (some weird 3.3v thing was happening) and added esp32
    [main.brd, main.sch]
2018-01-27 added in new gnd symbols (doesn't default to 3.3v anymore); added in esp32 library
    [main.brd, main.sch]
2018-01-29 Did IMU and most of UART
    [main.brd, main.sch]
2018-01-31 mosfet for laser
    [main.brd, main.sch]
2018-01-31 wired up almost all of esp's peripherals
    [main.brd, main.sch]
2018-02-06 more esp pins and isolating grounds
    [main.brd, main.sch]
2018-02-07 added schmitt trigger
    [main.brd, main.sch]
2018-02-07 finished schematic (draft1)
    [main.brd, main.sch]
2018-02-08 layout done! (minus sheep image)
    Still need to add sheep and check with tolerances of wherever we fab at,
    but otherwise done!!!!
    [main.brd, main.sch]
2018-02-09 added sheep
    [main.brd]
2018-02-10 fixed silkscreen (tPlace, tNames, tValues)
    [main.brd]
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2018-02-21 mechanical (solidworks) files moved to repo
    [Backup (1) of Base 4.0 v9.SLDPRT, Backup (1) of mechOverview.SLDASM, Backup (1) of thirdPlaceholder.SLDPRT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]
2018-02-21 began turret assm redesign, resized turret, added new cuts for: sg90 mount point, wires
    [Backup (1) of turret.SLDASM, Backup (1) of turretAcryllic.SLDPRT, Backup (1) of turretBody.SLDPRT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]
2018-02-22 more mech stuff
    [cross.SLDASM, turretBottom.SLDPRT, turretMaster_mk3.SLDPRT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]
2018-02-22 turret redesign done
    [master.SLDASM, turretBottom.SLDPRT, turretDiffuser.SLDPRT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]
2018-02-24 finished battery cap
    [AA Battery.SLDPRT, Base 4.0 v10.SLDPRT, Base 4.0 v10_mk2.SLDPRT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]
2018-02-25 completely finished assembly
    some bugs noticed:
    -wheel assembly has weird references to Assm1 or something like that
    -turret axis mate doesn't play well with other mates
    [Part13.sldprt, Part4.sldprt, SG90 - Micro Servo 9g - Tower Pro.1.SLDPRT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]
2018-02-26 added colors and finished constraining final model; organized schematic
    [bodyTop.sldprt, body_mk3.sldprt, main.brd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]
2018-02-27 fixes to battery holder, screw post adjustments for DC motor
    [batteryCap.SLDPRT, batteryHousing.SLDASM, bodyTop.sldprt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]
2018-03-04 converted battery holder to be detachable cantilevers (ie functional); (hopefully) toleranced turret bottom properly, need to confirm then will tolerance mid and top section (only need to tolerance p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
    [batteryCant.SLDPRT, batteryCant.STL, batteryCap.SLDPRT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]
2018-03-07 all turret adjustments should be good, potentially need to shrink turret to fit within wheel clearance; made rest of body parts detacheable cantilevers
    [Part4.sldprt, Top Cover.sldprt, batteryCant.SLDPRT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]
2018-03-08 batteryCant_01mm is actually a good pressfit when printed on T3 Land Factory in conjunction with female parts
    [batteryCant_01mm.SLDPRT, batteryCant_01mm.STL, bodyTop.STL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]
2018-03-08 solidworks garbage collection
    [turretMid.SLDPRT, turret_mk3.SLDASM]
2018-03-09 editted part layouts. changed pins for uart
    [main.brd, main.sch]
2018-03-12 body is print ready with all fasteners
    [board.SLDPRT, body_mk3.STL, body_mk3.sldprt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]
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2018-03-19 wheel fix
    [Backup (1) of body_mk3.sldprt, Backup (1) of pcbHolder_mk3.sldprt, Backup (1) of protoBody.SLDASM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]
2018-03-20 fix for bodyTop turret wire slots
    [bodyTop.SLDASM, bodyTop.STL, bodyTop.sldprt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]
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2018-03-21 fixes for rev2
    fixed mounting holes, connector overlap, added 6th pin for jtag,
    isolated 3rd switch pin, and added push button for IO0
    [main.brd]
2018-03-21 moved sheepy
    [main.brd]
2018-03-21 cable space fix
    The bottom of the body *will* need to be cut more to take advantage of the cable space fix
    [batteryCapDetachableInclCant.SLDASM, batteryHousing.SLDASM, batteryHousingDetachable.SLDASM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]
2018-03-21 extended hole body
    to complement the last commit
    [body_mk3.STL, body_mk3.sldprt, protoBody.SLDASM]
2018-03-21 camera holder
    [Camera Standoff v2.step, Camera holder top v2.step, Camera holder v5.step]
2018-03-21 camera name
    [Camera Standoff v2.step, Camera holder top v2.step, Camera holder v5.step]
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2018-03-22 turret fixed for electrical things; camera fixed and printed
    [Camera Standoff v2.STL, Camera holder top v2.SLDPRT, Camera holder top v2.STL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]
2018-03-24 new camera holder with 3 attachment points, new pcbHolder for pcb rev2
    [Camera holder v7.step, Camera holder v7s.SLDPRT, Camera holder v7s.STL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]
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2018-04-02 unity from allnighter; frontWeightContainer created; added motor model from grabcad; began omniwheel
    [Moto Reductor - Rueda.SLDASM, Moto Reductor 01.SLDPRT, Rueda 01.SLDPRT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]
2018-04-02 finished omniwheel w/ appropriate mods to pcbHolder
    [body_mk3.sldprt, omniBackSupport.sldprt, omniBall.sldprt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]
2018-04-04 modded bodyTop for dual extrusion CV; designed omniWheel; misc commits
    [bodyTop.SLDASM, bodyTop.STL, bodyTop.sldprt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]
2018-04-04 bodyTop M600 gcode mod
    removed useless .amf file
    [bodyTopCV.AMF]
2018-04-04 increased cv pattern depth to 0.5mm; added omni ball stl; modded turret top for vertical LED
    [bodyTop.SLDASM, bodyTop.sldprt, bodyTopCV - bodyTop-1.STL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]
2018-04-06 finished designing mk4 turret
    [SG90 - Micro Servo 9g - Tower Pro.1.SLDPRT, protoBody.SLDASM, quadFin.sldprt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]
2018-04-06 fixed quadfin tolerance, led recess, gun recess
    [quadFin.sldprt, turretGround.SLDPRT, turretLevel1.sldprt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]
2018-04-08 lots of tiny fixes for the turret to make it work proper; also managed to tweak settings for omni so TPU actually prints properly
    [body_mk3.sldprt, omniBall.STL, omniBall.sldprt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]
2018-04-08 omni will use 1.75 filament for core
    [body_mk3.sldprt, omniBall.STL, omniBall.sldprt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]
2018-04-08 can't remember; probably tolerancing
    [Backup (1) of turretGun_fromMk3.SLDPRT, Backup (1) of turret_mk4.SLDASM, Backup (2) of turret_mk4.SLDASM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]
2018-04-09 made a lot of changes to body for mk3.5 (though I'm not renamign directrories for that); this is in prep for the new turret; also need to modify turret so bolts come in from top not bottom (too diffi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
    [Backup (1) of body_mk3.sldprt, Backup (1) of pcbHolder_mk3.sldprt, Backup (1) of protoBody.SLDASM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]
2018-04-09 made bolt changes to turret mk4 and enlarged turret if I didn't already
    [Backup (1) of turret_mk4.SLDASM, Backup (2) of turret_mk4.SLDASM, Backup (3) of turret_mk4.SLDASM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]
2018-04-10 added all the backups and the new things too
    [Backup (1) of bodyTop.SLDASM, Backup (1) of bodyTop.sldprt, Backup (1) of bodyTopTurret.sldprt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]
2018-04-10 moar chassis compatiblity; split into 2 sectinos almost done; added slots to sides; created hooks for sides; had to fix front weight contain
    [Backup (1) of attachHook.sldprt, Backup (1) of attachPoint.sldprt, Backup (1) of attachPointASM.SLDASM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]
2018-04-10 DONNEEEE; chassis should be compatible with new turret; new cv top too
    [Backup (1) of bodyTop.SLDASM, Backup (1) of bodyTopCV.sldprt, Backup (1) of bodyTopCVASM.SLDASM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]
2018-04-10 rev 2 board
    gerbers and such for second version of board
    [main.brd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]
2018-04-11 move with small corrections
    [udp.c]
2018-04-12 reduced z variance correction distance from 1mm to 0.2mm
    [quadFin.sldprt, turretGround.SLDPRT, turretLevel1.sldprt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]
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2018-04-13 designed camera stabilizer (39mm); designed new batteryHolder; updated bodyTopTurret
    [batteryCapDetachable.SLDPRT, batteryCapDetachableInclCant.SLDASM, batteryCap_mk3.5.SLDPRT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]
2018-04-15 battery stuff; bodyTopTurret fix
    [batteryHousing_mk3.5.SLDASM, batteryShell_mk3.5.sldprt, bodyTopTurret.sldprt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]
2018-04-17 all the unity stuff charles has bene doing; new photo resistor adapter, fixed led cover
    [newPhotoAdapt.STL, newPhotoAdapt.sldprt, newPhotoAdaptASM.SLDASM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]
2018-04-23 omni wheel changes (not really a wheel anymore mk3.5); manufacturing fixes for turretGun and turretGround (apparently we were modeling off the wrong fin (Tower Pro vs FITEC)
    [SG90 - Micro Servo 9g - Tower Pro.1.SLDPRT, SG90 - Micro Servo 9g - Tower Pro.3.SLDPRT, SG90 - Micro Servo 9g - Tower Pro.5.SLDPRT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]
2018-04-23 minor change to pcbHolder
    [Backup (1) of bodyTop.SLDASM, Backup (1) of bodyTopCV.sldprt, Backup (1) of body_mk3.sldprt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]
2018-04-23 stabilizerClip from 39mm to 37mm, added clip feature; some updated gcode
    [Backup (1) of attachPoint.sldprt, Backup (1) of stabilizerClip_37mm.SLDPRT, Backup (2) of stabilizerClip_37mm.SLDPRT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]
2018-04-24 added new layer to turret to fix bulge caused by fin screw
    [Backup (1) of turretLevel1.sldprt, Backup (1) of turret_mk4.SLDASM, Backup (2) of turretLevel1.sldprt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]
2018-04-24 commiting new unity
    [MethodMap.tsv]
2018-04-24 turret tracking working
    [MethodMap.tsv]

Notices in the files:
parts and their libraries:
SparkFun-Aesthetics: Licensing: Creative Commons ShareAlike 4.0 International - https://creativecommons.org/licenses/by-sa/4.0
